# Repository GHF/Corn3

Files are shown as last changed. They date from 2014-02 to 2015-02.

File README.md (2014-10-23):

Corn3
=====
Copyright (C) 2014 Xo Wang

Corn3 is firmware for Corntroller version 3. It is a total rewrite of previous
Corntroller code, with a focus on writing code and documentation that may serve
as an introduction to three phase motor control for hobbyists.

Build
-----
Corn3 is written for use with GNU Tools for ARM Embedded Processors
(https://launchpad.net/gcc-arm-embedded).

To build, run make:

```
make
```

If you don't have arm-none-eabi in your PATH, specify its prefix in TRGT, e.g.:

```
make TRGT=~/gcc-arm-none-eabi-4_8-2014q3/bin/arm-none-eabi-
```

Hardware
--------
Corntroller is a small and efficient brushless motor controller.

Version 3.2 features:

  - 0.8 in by 1.6 in
  - STM32F3 microcontroller (ARM Cortex-M4 @ 72MHz)
  - TI DRV8301 gate driver, current sense amplifier, and buck converter
  - Three-phase inverter with SO8 N-FETs
  - Dual shunt current sense
  - Hall sensor inputs
  - Up to 30 V input voltage

No power figures available, but should be similar to hobby controllers of
similar size.

Hacking
-------
Corn3 and Corntroller are developed using the Black Magic Probe debugger.

See http://www.blacksphere.co.nz/main/blackmagic

Corntroller v3 has a 10-pin "mini" keyed JTAG header and a PicoBlade 4-pin
serial debug connector. The firmware does not yet support USB firmware
flashing.

License
-------
Corn3 is licensed under the MIT license with non-advertisement clause.

In compliance with the Apache license that ChibiOS configuration and low level
drivers are licensed under, the Apache License version 2.0 is included.

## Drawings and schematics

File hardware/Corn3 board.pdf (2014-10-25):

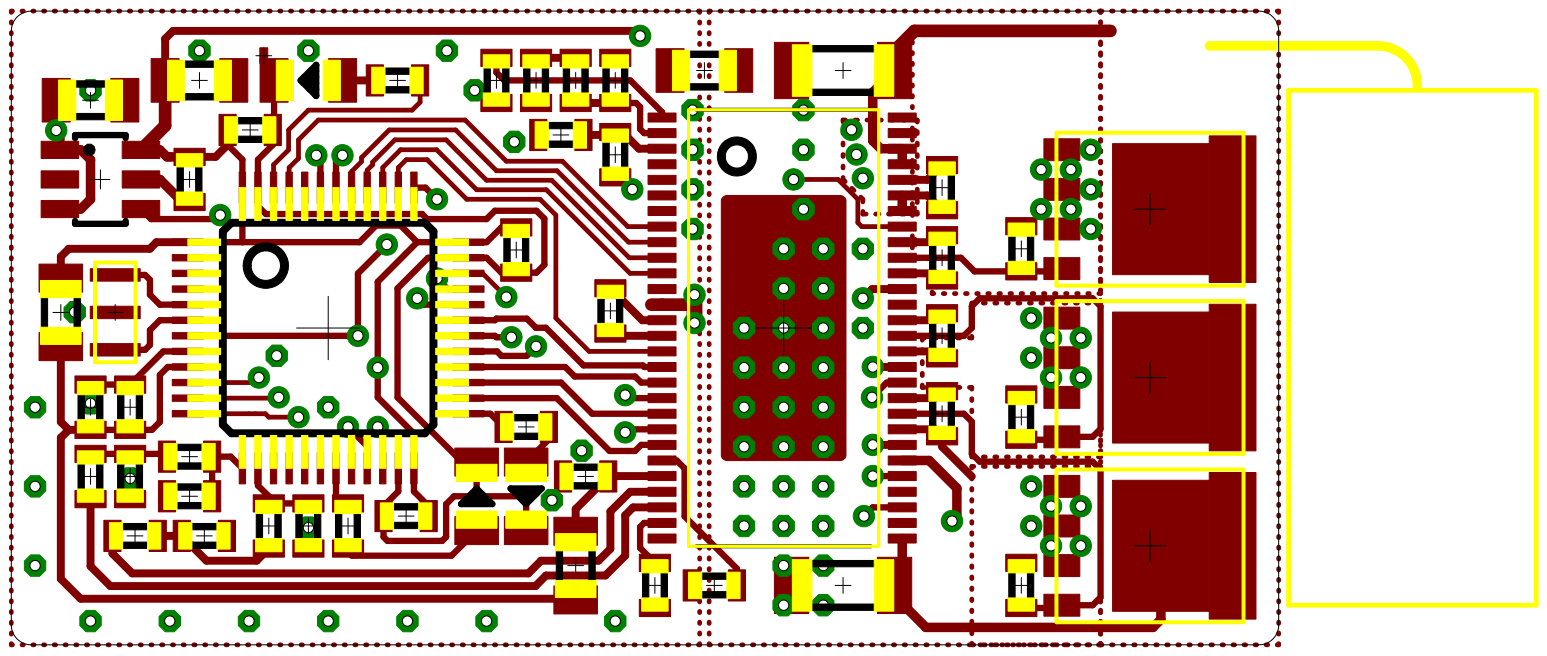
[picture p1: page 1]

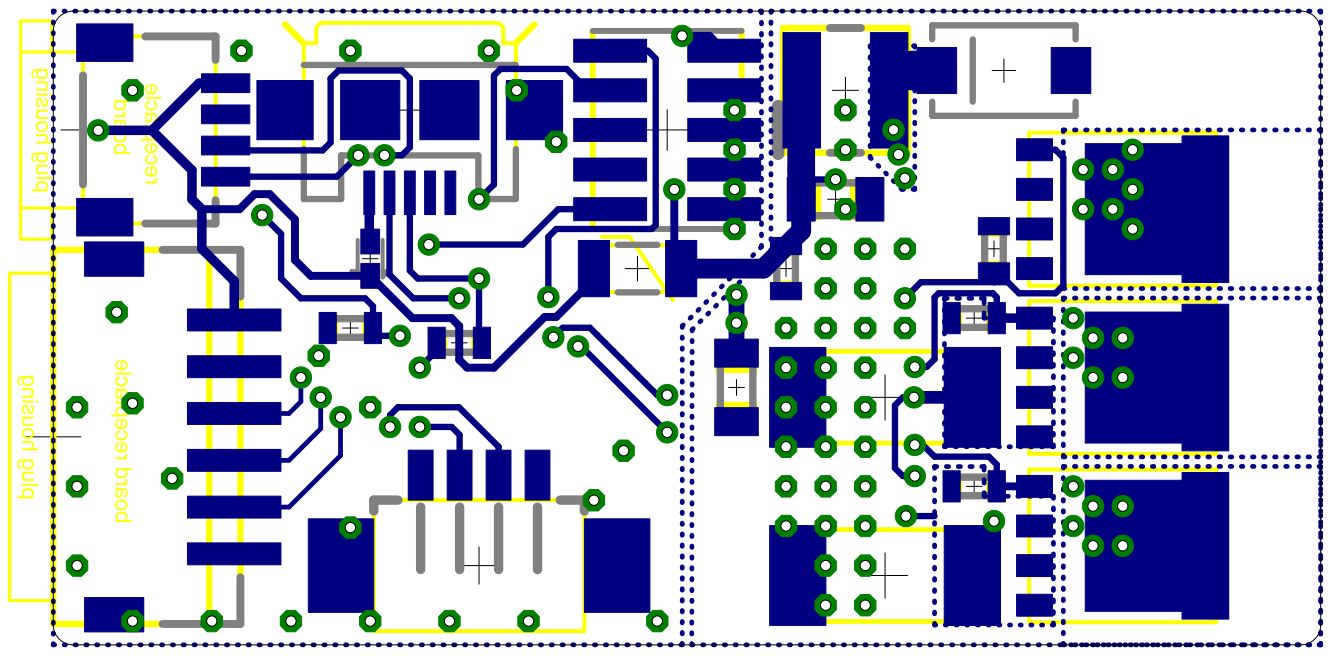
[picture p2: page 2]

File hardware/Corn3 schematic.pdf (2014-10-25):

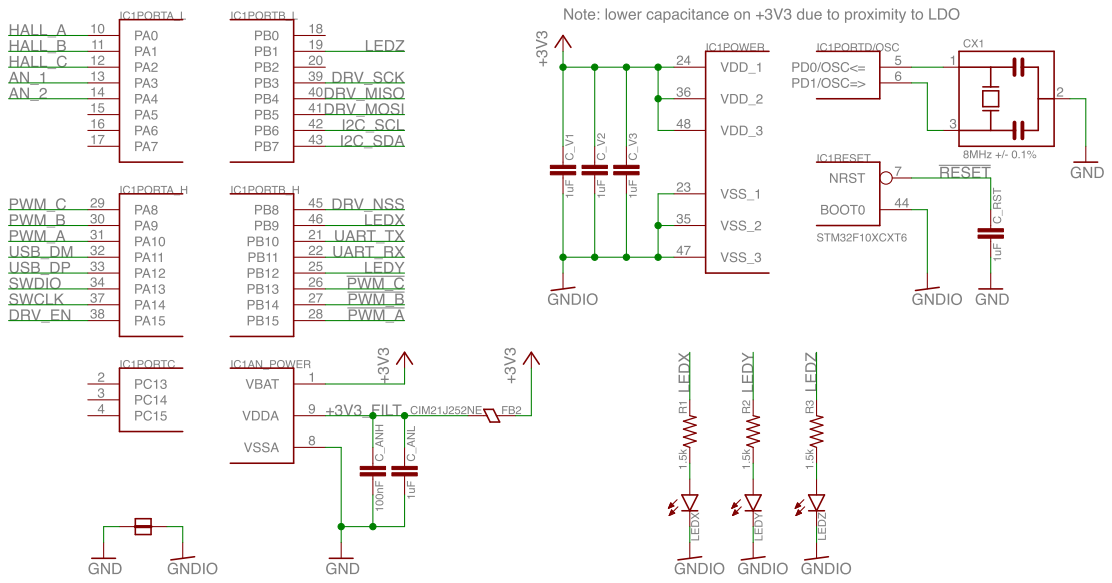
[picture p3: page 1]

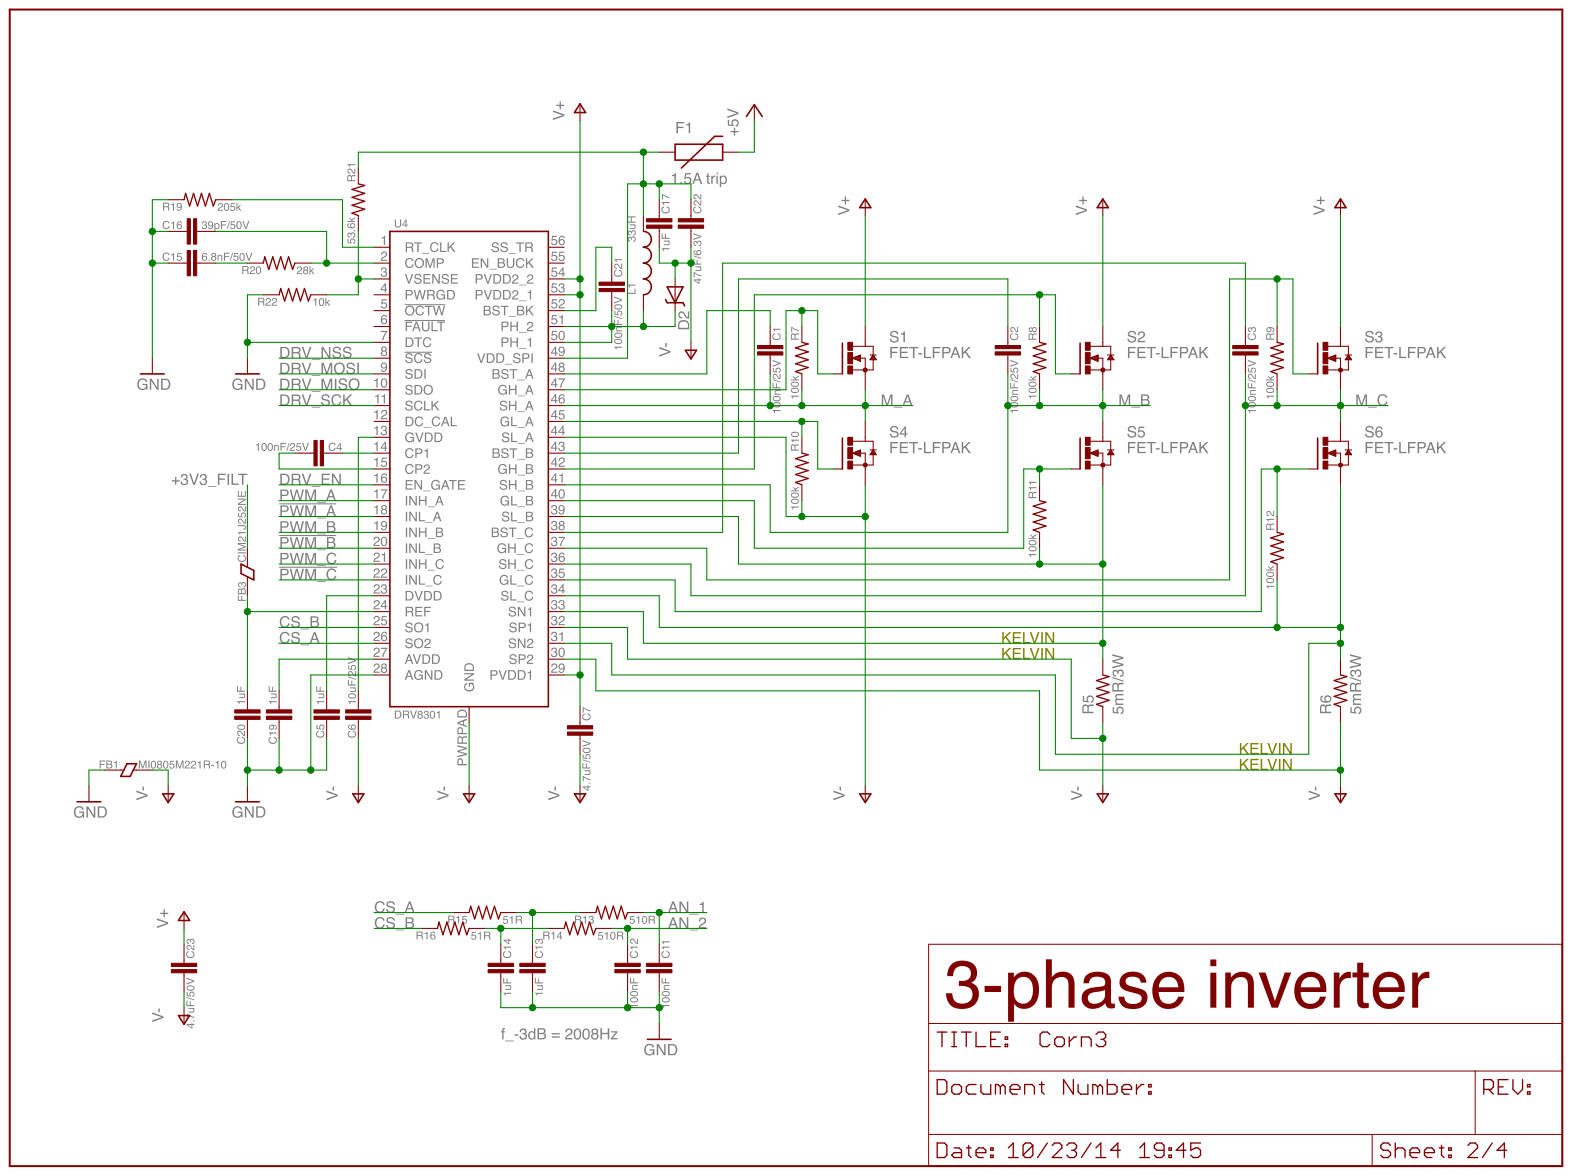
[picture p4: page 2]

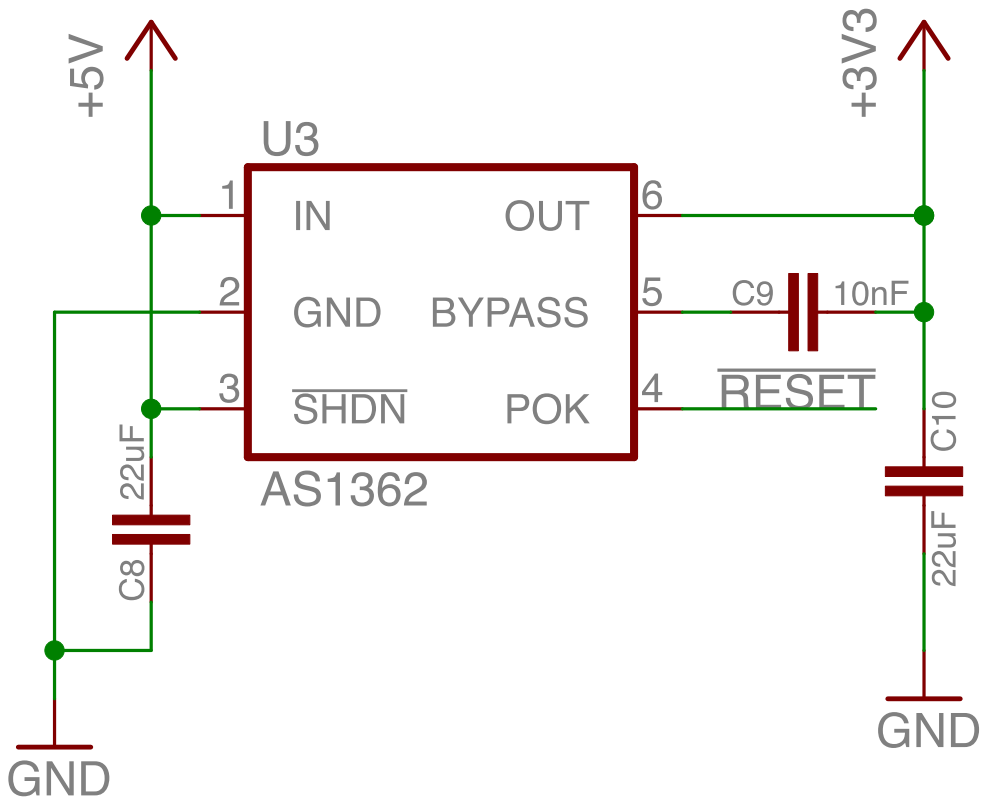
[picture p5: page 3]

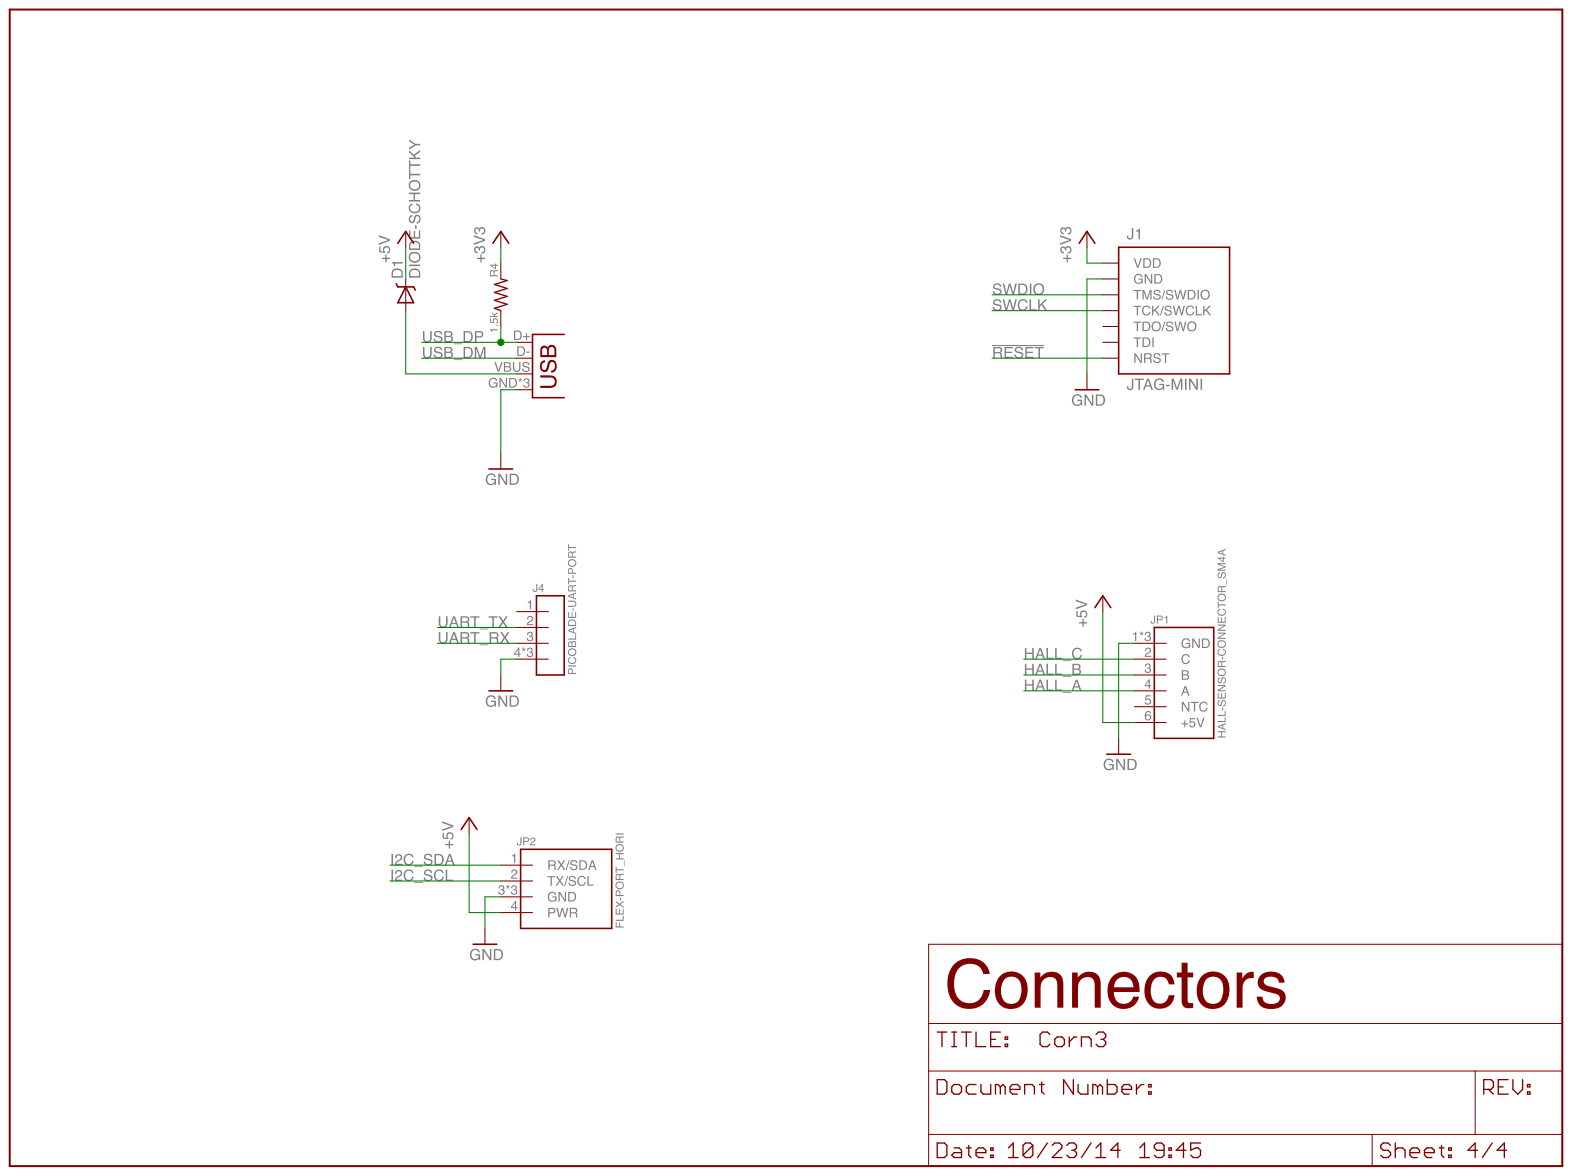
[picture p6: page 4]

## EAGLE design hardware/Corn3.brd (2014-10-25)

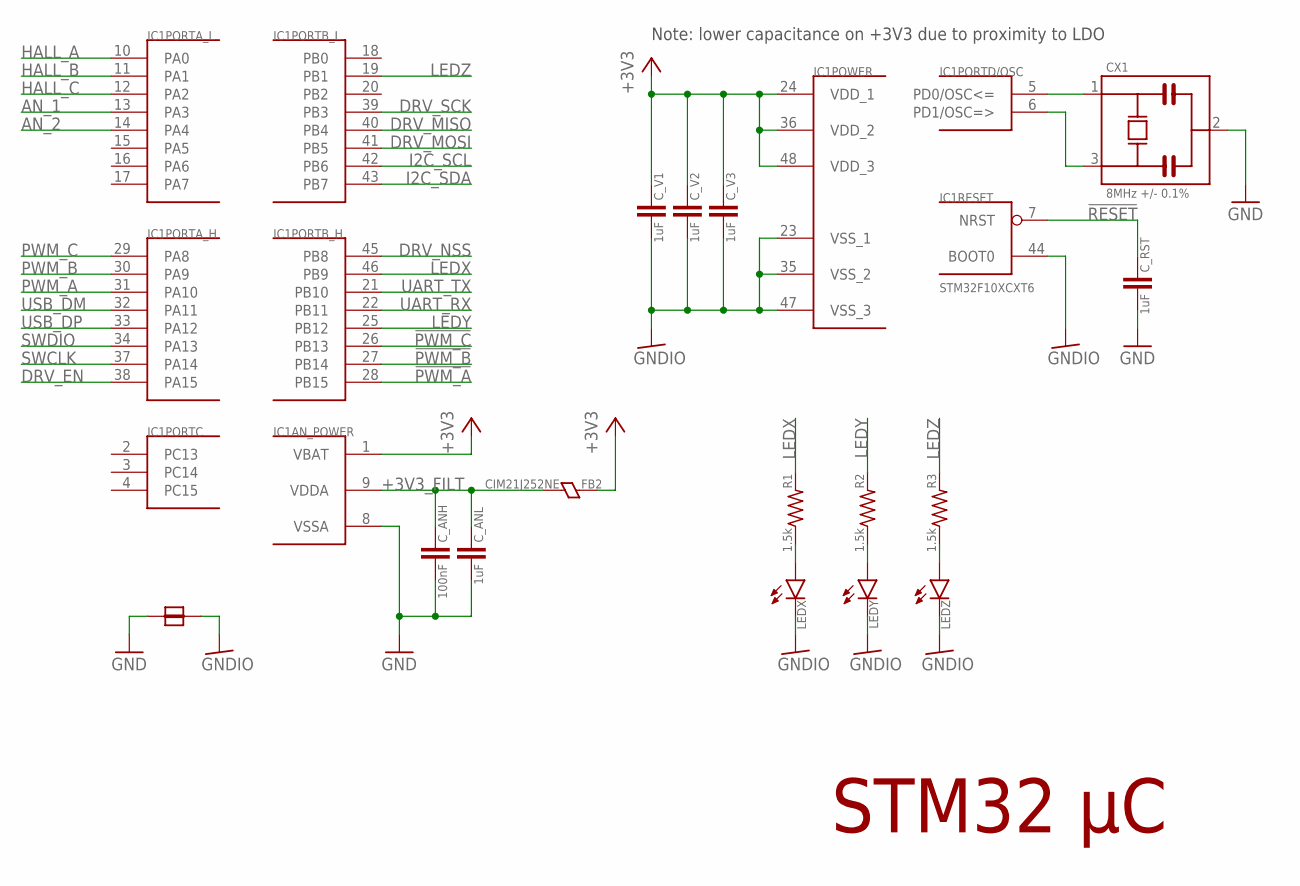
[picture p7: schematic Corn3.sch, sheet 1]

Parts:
CX1: 8MHz +/- 0.1%; MURATA_CSTCE
C_ANH: 100nF; 0603
C_ANL: 1uF; 0603
C_RST: 1uF; 0603
C_V1, C_V2, C_V3: 1uF; 0603
FB2: CIM21J252NE; 0805
IC1: STM32F10XCXT6; TQFP48
JUMPER-GND-GNDIO: JUMPER5025; 5025
LEDX: LED0805; 0805_POL
LEDY: LED0805; 0805_POL
LEDZ: LED0805; 0805_POL
R1, R2, R3: 1.5k; 0603

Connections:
!PWM_A: IC1.28 (PB15); also elsewhere on the board
!PWM_B: IC1.27 (PB14); also elsewhere on the board
!PWM_C: IC1.26 (PB13); also elsewhere on the board
!RESET: C_RST.1, IC1.7 (NRST); also elsewhere on the board
+3V3: C_V1.1, C_V2.1, C_V3.1, FB2.2, IC1.1 (VBAT), IC1.24 (VDD_1), IC1.36 (VDD_2), IC1.48 (VDD_3); also elsewhere on the board
+3V3_FILT: C_ANH.1, C_ANL.1, FB2.1, IC1.9 (VDDA); also elsewhere on the board
AN_1: IC1.13 (PA3); also elsewhere on the board
AN_2: IC1.14 (PA4); also elsewhere on the board
DRV_EN: IC1.38 (PA15); also elsewhere on the board
DRV_MISO: IC1.40 (PB4); also elsewhere on the board
DRV_MOSI: IC1.41 (PB5); also elsewhere on the board
DRV_NSS: IC1.45 (PB8); also elsewhere on the board
DRV_SCK: IC1.39 (PB3); also elsewhere on the board
GND: CX1.2, C_ANH.2, C_ANL.2, C_RST.2, IC1.8 (VSSA), JUMPER-GND-GNDIO.1; also elsewhere on the board
GNDIO: C_V1.2, C_V2.2, C_V3.2, IC1.23 (VSS_1), IC1.35 (VSS_2), IC1.44 (BOOT0), IC1.47 (VSS_3), JUMPER-GND-GNDIO.2, LEDX.- (C), LEDY.- (C), LEDZ.- (C)
HALL_A: IC1.10 (PA0); also elsewhere on the board
HALL_B: IC1.11 (PA1); also elsewhere on the board
HALL_C: IC1.12 (PA2); also elsewhere on the board
I2C_SCL: IC1.42 (PB6); also elsewhere on the board
I2C_SDA: IC1.43 (PB7); also elsewhere on the board
LEDX: IC1.46 (PB9), R1.2
LEDY: IC1.25 (PB12), R2.2
LEDZ: IC1.19 (PB1), R3.2
unnamed: CX1.3, IC1.6 (PD1/OSC=>)
unnamed: CX1.1, IC1.5 (PD0/OSC<=)
unnamed: LEDX.+ (A), R1.1
unnamed: LEDZ.+ (A), R3.1
unnamed: LEDY.+ (A), R2.1
PWM_A: IC1.31 (PA10); also elsewhere on the board
PWM_B: IC1.30 (PA9); also elsewhere on the board
PWM_C: IC1.29 (PA8); also elsewhere on the board
SWCLK: IC1.37 (PA14); also elsewhere on the board
SWDIO: IC1.34 (PA13); also elsewhere on the board
UART_RX: IC1.22 (PB11); also elsewhere on the board
UART_TX: IC1.21 (PB10); also elsewhere on the board
USB_DM: IC1.32 (PA11); also elsewhere on the board
USB_DP: IC1.33 (PA12); also elsewhere on the board

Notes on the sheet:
STM32 µC
Note: lower capacitance on +3V3 due to proximity to LDO

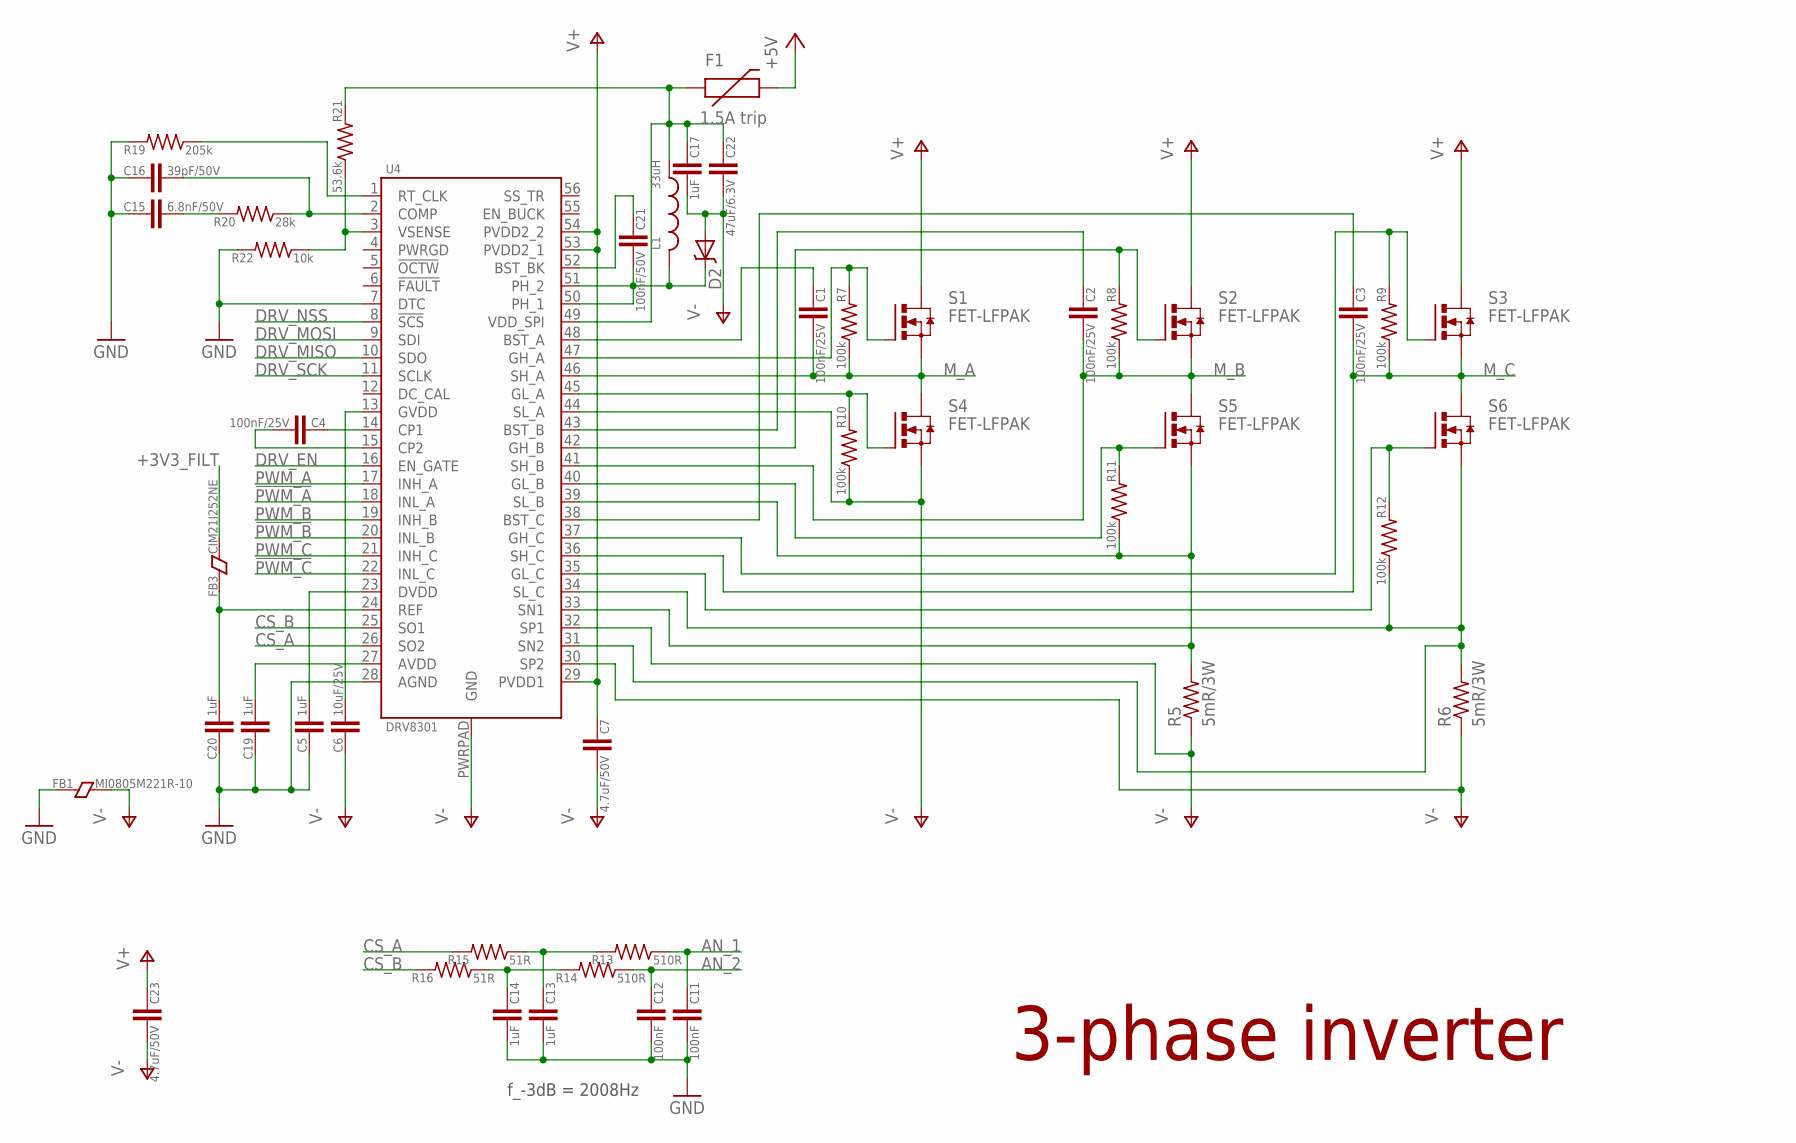
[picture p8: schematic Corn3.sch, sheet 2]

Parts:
C1, C2, C3, C4: 100nF/25V; 0603
C5, C13, C14, C17, C19, C20: 1uF; 0603
C6: 10uF/25V; 0805
C7, C23: 4.7uF/50V; 1206
C11, C12: 100nF; 0603
C15: 6.8nF/50V; 0603
C16: 39pF/50V; 0603
C21: 100nF/50V; 0603
C22: 47uF/6.3V; 0805
D2: DIODE-SCHOTTKY_; SMA-DIODE
F1: 1.5A trip; PTC-1206
FB1: MI0805M221R-10; 0805
FB3: CIM21J252NE; 0805
L1: 33uH; TAIYO-YUDEN_NR40
R5, R6: 5mR/3W; R2512
R7, R8, R9, R10, R11, R12: 100k; 0603
R13, R14: 510R; 0603
R15, R16: 51R; 0603
R19: 205k; 0603
R20: 28k; 0603
R21: 53.6k; 0603
R22: 10k; 0603
S1, S2, S3, S4, S5, S6: FET-LFPAK; SON-5X6
U4: DRV8301; HTSSOP-56

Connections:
!PWM_A: U4.18 (INL_A); also elsewhere on the board
!PWM_B: U4.20 (INL_B); also elsewhere on the board
!PWM_C: U4.22 (INL_C); also elsewhere on the board
+3V3_FILT: FB3.1; also elsewhere on the board
+5V: F1.2; also elsewhere on the board
AN_1: C11.1, R13.1; also elsewhere on the board
AN_2: C12.1, R14.1; also elsewhere on the board
CS_A: R15.2, U4.26 (SO2)
CS_B: R16.2, U4.25 (SO1)
DRV_EN: U4.16 (EN_GATE); also elsewhere on the board
DRV_MISO: U4.10 (SDO); also elsewhere on the board
DRV_MOSI: U4.9 (SDI); also elsewhere on the board
DRV_NSS: U4.8 (!SCS); also elsewhere on the board
DRV_SCK: U4.11 (SCLK); also elsewhere on the board
GND: C5.1, C11.2, C12.2, C13.2, C14.2, C15.1, C16.1, C19.1, C20.1, FB1.2, R19.2, R22.2, U4.7 (DTC), U4.28 (AGND); also elsewhere on the board
M_A: C1.2, R7.1, S1.S1 (S), S1.S2 (S), S1.S3 (S), S4.D, S4.D_ (D), U4.46 (SH_A)
M_B: C2.2, R8.1, S2.S1 (S), S2.S2 (S), S2.S3 (S), S5.D, S5.D_ (D), U4.41 (SH_B)
M_C: C3.2, R9.1, S3.S1 (S), S3.S2 (S), S3.S3 (S), S6.D, S6.D_ (D), U4.36 (SH_C)
unnamed: R8.2, S2.G, U4.42 (GH_B)
unnamed: R7.2, S1.G, U4.47 (GH_A)
unnamed: R12.2, S6.G, U4.35 (GL_C)
unnamed: R11.2, S5.G, U4.40 (GL_B)
unnamed: R9.2, S3.G, U4.37 (GH_C)
unnamed: C21.1, U4.52 (BST_BK)
unnamed: C1.1, U4.48 (BST_A)
unnamed: C2.1, U4.43 (BST_B)
unnamed: C3.1, U4.38 (BST_C)
unnamed: R10.2, S4.G, U4.45 (GL_A)
unnamed: C17.1, C22.1, F1.1, L1.1, R21.2, U4.49 (VDD_SPI)
unnamed: C16.2, R20.1, U4.2 (COMP)
unnamed: C14.1, R14.2, R16.1
unnamed: C13.1, R13.2, R15.1
unnamed: C15.2, R20.2
unnamed: R21.1, R22.1, U4.3 (VSENSE)
unnamed: C5.2, U4.23 (DVDD)
unnamed: C6.2, U4.13 (GVDD)
unnamed: C4.1, U4.14 (CP1)
unnamed: C4.2, U4.15 (CP2)
unnamed: C21.2, D2.C, L1.2, U4.50 (PH_1), U4.51 (PH_2)
unnamed: C20.2, FB3.2, U4.24 (REF)
unnamed: C19.2, U4.27 (AVDD)
unnamed: R19.1, U4.1 (RT_CLK)
PWM_A: U4.17 (INH_A); also elsewhere on the board
PWM_B: U4.19 (INH_B); also elsewhere on the board
PWM_C: U4.21 (INH_C); also elsewhere on the board
SL_B: R5.2, R11.1, S5.S1 (S), S5.S2 (S), S5.S3 (S), U4.33 (SN1), U4.39 (SL_B)
SL_C: R6.2, R12.1, S6.S1 (S), S6.S2 (S), S6.S3 (S), U4.31 (SN2), U4.34 (SL_C)
V+: C7.1, C23.1, S1.D, S1.D_ (D), S2.D, S2.D_ (D), S3.D, S3.D_ (D), U4.29 (PVDD1), U4.53 (PVDD2_1), U4.54 (PVDD2_2)
V-: C6.1, C7.2, C17.2, C22.2, C23.2, D2.A, FB1.1, R5.1, R6.1, R10.1, S4.S1 (S), S4.S2 (S), S4.S3 (S), U4.30 (SP2), U4.32 (SP1), U4.44 (SL_A), U4.PWRPAD (GND)

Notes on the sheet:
3-phase inverter
f_-3dB = 2008Hz

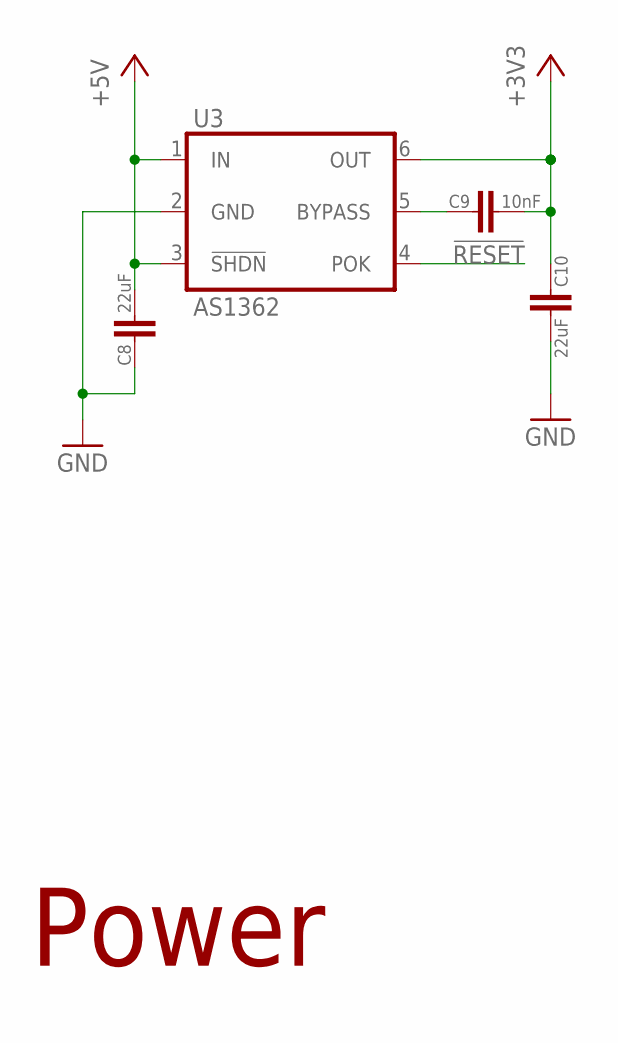
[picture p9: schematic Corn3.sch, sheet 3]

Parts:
C8, C10: 22uF; 0805
C9: 10nF; 0603
U3: AS1362; SOT23-6

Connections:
!RESET: U3.4 (POK); also elsewhere on the board
+3V3: C9.2, C10.1, U3.6 (OUT); also elsewhere on the board
+5V: C8.2, U3.1 (IN), U3.3 (!SHDN); also elsewhere on the board
GND: C8.1, C10.2, U3.2 (GND); also elsewhere on the board
unnamed: C9.1, U3.5 (BYPASS)

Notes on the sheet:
Power

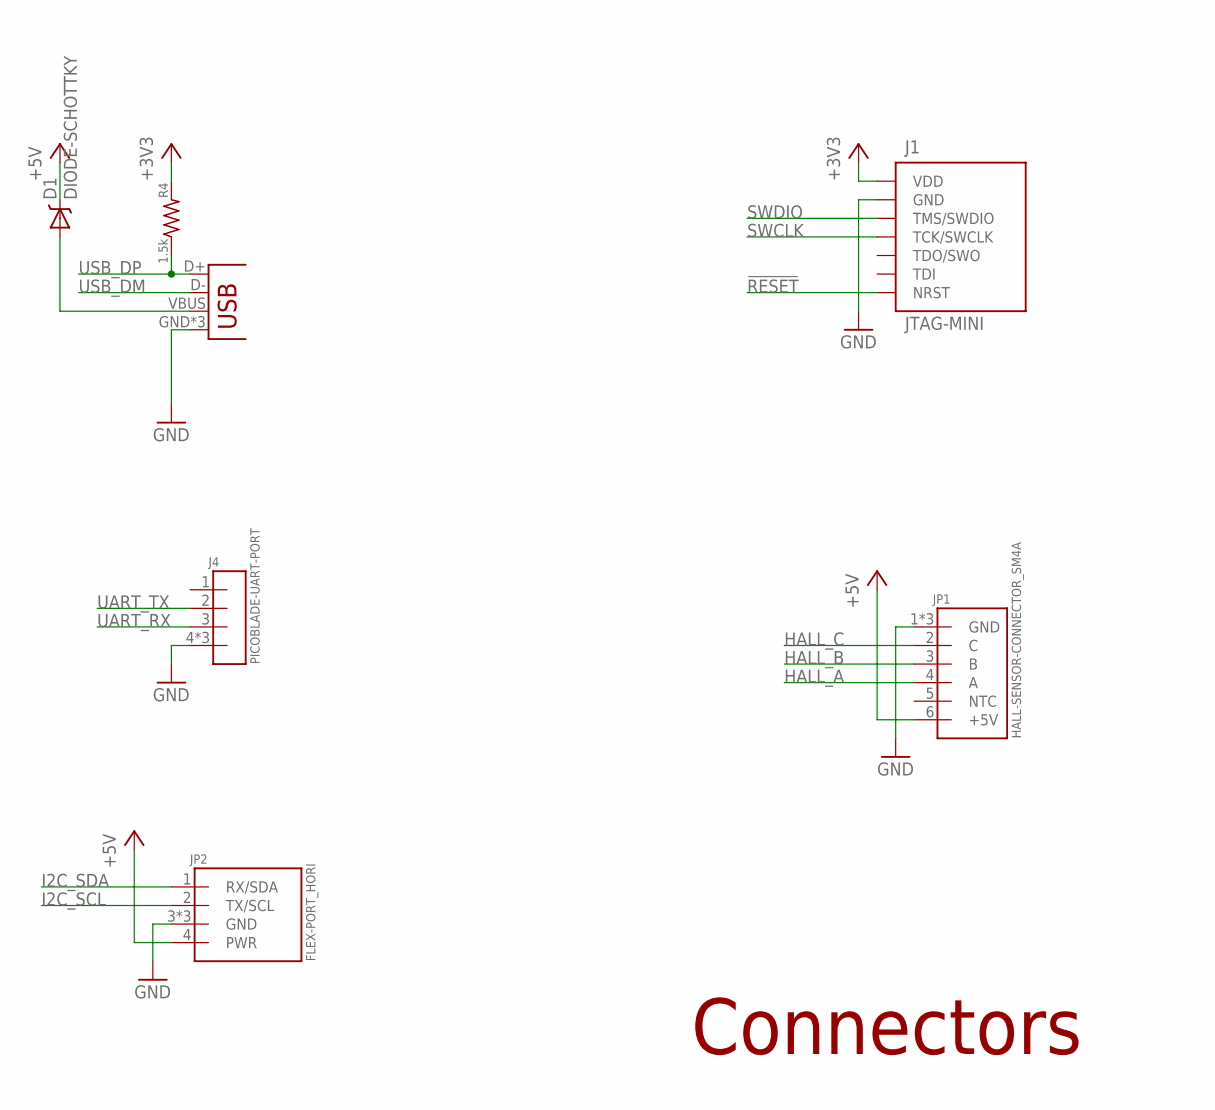
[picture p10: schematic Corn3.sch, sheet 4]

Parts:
D1: DIODE-SCHOTTKY; SOD-523
J1: JTAG-MINI
J4: PICOBLADE-UART-PORT; PICOBLADE-04-SMD-RA
JP1: HALL-SENSOR-CONNECTOR_SM4A; JST_S6B-ZR-SM4A
JP2: FLEX-PORT_HORI; JST_SM04B-SRSS
JP3: USB-MICROB
R4: 1.5k; 0603

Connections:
!RESET: J1.NRST; also elsewhere on the board
+3V3: J1.VDD, R4.2; also elsewhere on the board
+5V: D1.C, JP1.6 (+5V), JP2.4 (PWR); also elsewhere on the board
GND: J1.GND1 (GND), J1.GND2 (GND), J1.GND3 (GND), J1.GND4 (GND), J4.4, J4.TAB1 (4), J4.TAB2 (4), JP1.1 (GND), JP1.TAB1 (GND), JP1.TAB2 (GND), JP2.3 (GND), JP2.TAB1 (GND), JP2.TAB2 (GND), JP3.GND, JP3.MT1 (GND), JP3.MT2 (GND); also elsewhere on the board
HALL_A: JP1.4 (A); also elsewhere on the board
HALL_B: JP1.3 (B); also elsewhere on the board
HALL_C: JP1.2 (C); also elsewhere on the board
I2C_SCL: JP2.2 (TX/SCL); also elsewhere on the board
I2C_SDA: JP2.1 (RX/SDA); also elsewhere on the board
unnamed: D1.A, JP3.VBUS
SWCLK: J1.TCK (TCK/SWCLK); also elsewhere on the board
SWDIO: J1.TMS (TMS/SWDIO); also elsewhere on the board
UART_RX: J4.3; also elsewhere on the board
UART_TX: J4.2; also elsewhere on the board
USB_DM: JP3.D-; also elsewhere on the board
USB_DP: JP3.D+, R4.1; also elsewhere on the board

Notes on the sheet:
Connectors

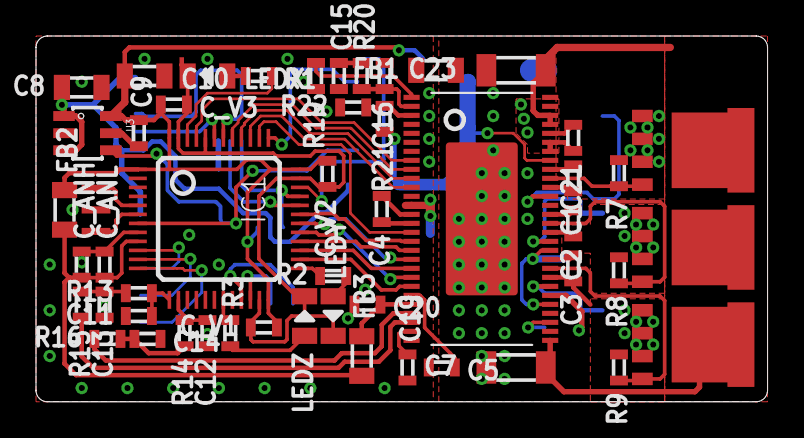
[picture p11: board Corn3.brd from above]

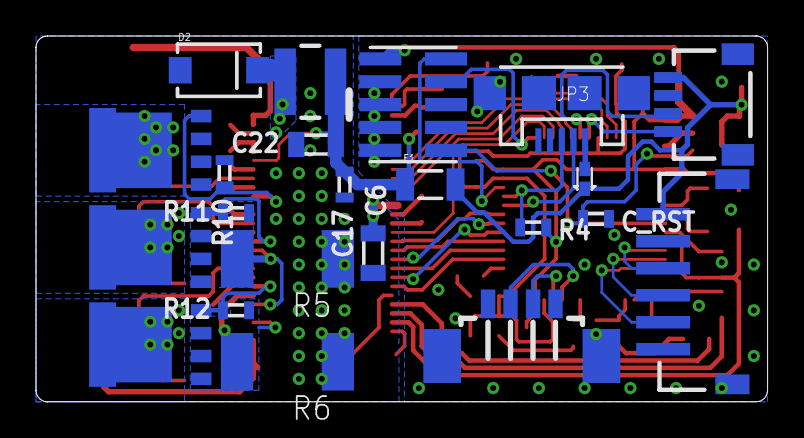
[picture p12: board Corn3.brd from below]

Board: 2 copper layers, 40.6 x 20.3 mm, 74 parts (22 on the bottom side), 73 nets.

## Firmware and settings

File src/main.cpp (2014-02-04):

/*
 * Corn3 - Copyright (C) 2014 Xo Wang
 *
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
 * Except as contained in this notice, the name(s) of the above copyright
 * holders shall not be used in advertising or otherwise to promote the sale,
 * use or other dealings in this Software without prior written authorization.
 */

#include <cstdlib>

#include "ch.h"
#include "hal.h"

#include "corn.h"

int main(void) {
  halInit();
  chSysInit();

  Corn corn;
  corn.Start();
  corn.MainLoop();

  return EXIT_SUCCESS;
}

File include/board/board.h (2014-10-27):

/*
 * Corn3 - Copyright (C) 2014 Xo Wang
 * ChibiOS/RT - Copyright (C) 2006-2013 Giovanni Di Sirio (MODIFIED BY ABOVE)
 *
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
 * Except as contained in this notice, the name(s) of the above copyright
 * holders shall not be used in advertising or otherwise to promote the sale,
 * use or other dealings in this Software without prior written authorization.
 */

#ifndef BOARD_BOARD_H_
#define BOARD_BOARD_H_

/*
 * Setup for the Corntroller brushless motor controller.
 */

/*
 * Board oscillators-related settings.
 * NOTE: LSE not fitted.
 */
#if !defined(STM32_LSECLK)
#define STM32_LSECLK                0
#endif

#define STM32_LSEDRV                (3 << 3)

#if !defined(STM32_HSECLK)
#define STM32_HSECLK                8000000
#endif

/*
 * MCU type as defined in the ST header.
 */
#define STM32F30X

/*
 * IO pins assignments.
 */
#define GPIOA_HALL_A                0
#define GPIOA_HALL_B                1
#define GPIOA_HALL_C                2
#define GPIOA_PIN3                  3
#define GPIOA_PIN4                  4
#define GPIOA_PIN5                  5
#define GPIOA_PIN6                  6
#define GPIOA_PIN7                  7
#define GPIOA_PWM_C                 8
#define GPIOA_PWM_B                 9
#define GPIOA_PWM_A                 10
#define GPIOA_USB_DM                11
#define GPIOA_USB_DP                12
#define GPIOA_SWDIO                 13
#define GPIOA_SWCLK                 14
#define GPIOA_DRV_EN                15

#define GPIOB_PIN0                  0
#define GPIOB_LEDZ                  1
#define GPIOB_PIN2                  2
#define GPIOB_DRV_SCK               3
#define GPIOB_DRV_MISO              4
#define GPIOB_DRV_MOSI              5
#define GPIOB_PWM_IN                6
#define GPIOB_PIN7                  7
#define GPIOB_DRV_NSS               8
#define GPIOB_LEDX                  9
#define GPIOB_UART_TX               10
#define GPIOB_UART_RX               11
#define GPIOB_LEDY                  12
#define GPIOB_PWM_CN                13
#define GPIOB_PWM_BN                14
#define GPIOB_PWM_AN                15

#define GPIOC_PIN0                  0
#define GPIOC_PIN1                  1
#define GPIOC_PIN2                  2
#define GPIOC_PIN3                  3
#define GPIOC_PIN4                  4
#define GPIOC_PIN5                  5
#define GPIOC_PIN6                  6
#define GPIOC_PIN7                  7
#define GPIOC_PIN8                  8
#define GPIOC_PIN9                  9
#define GPIOC_PIN10                 10
#define GPIOC_PIN11                 11
#define GPIOC_PIN12                 12
#define GPIOC_PIN13                 13
#define GPIOC_PIN14                 14
#define GPIOC_PIN15                 15

#define GPIOD_PIN0                  0
#define GPIOD_PIN1                  1
#define GPIOD_PIN2                  2
#define GPIOD_PIN3                  3
#define GPIOD_PIN4                  4
#define GPIOD_PIN5                  5
#define GPIOD_PIN6                  6
#define GPIOD_PIN7                  7
#define GPIOD_PIN8                  8
#define GPIOD_PIN9                  9
#define GPIOD_PIN10                 10
#define GPIOD_PIN11                 11
#define GPIOD_PIN12                 12
#define GPIOD_PIN13                 13
#define GPIOD_PIN14                 14
#define GPIOD_PIN15                 15

#define GPIOE_PIN0                  0
#define GPIOE_PIN1                  1
#define GPIOE_PIN2                  2
#define GPIOE_PIN3                  3
#define GPIOE_PIN4                  4
#define GPIOE_PIN5                  5
#define GPIOE_PIN6                  6
#define GPIOE_PIN7                  7
#define GPIOE_PIN8                  8
#define GPIOE_PIN9                  9
#define GPIOE_PIN10                 10
#define GPIOE_PIN11                 11
#define GPIOE_PIN12                 12
#define GPIOE_PIN13                 13
#define GPIOE_PIN14                 14
#define GPIOE_PIN15                 15

#define GPIOF_OSC_IN                0
#define GPIOF_OSC_OUT               1
#define GPIOF_PIN2                  2
#define GPIOF_PIN3                  3
#define GPIOF_PIN4                  4
#define GPIOF_PIN5                  5
#define GPIOF_PIN6                  6
#define GPIOF_PIN7                  7
#define GPIOF_PIN8                  8
#define GPIOF_PIN9                  9
#define GPIOF_PIN10                 10
#define GPIOF_PIN11                 11
#define GPIOF_PIN12                 12
#define GPIOF_PIN13                 13
#define GPIOF_PIN14                 14
#define GPIOF_PIN15                 15
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

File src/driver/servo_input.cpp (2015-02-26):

/*
 * Corn3 - Copyright (C) 2014 Xo Wang
 *
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
 * Except as contained in this notice, the name(s) of the above copyright
 * holders shall not be used in advertising or otherwise to promote the sale,
 * use or other dealings in this Software without prior written authorization.
 */

#include "driver/servo_input.h"

#include <algorithm>

#include "config.h"
#include "base/integer.h"
#include "base/log.h"
#include "base/utility.h"
#include "motor/commutator_six_step.h"

ServoInput::ServoInput(ICUDriver *icu_driver)
    : icu_driver_(icu_driver),
      commutator_six_step_(nullptr),
      num_overflows_(0),
      last_amplitude_(0) {
}

void ServoInput::Start() {
  icu_driver_->self = this;
  LogDebug("Configuring servo input capture at %u Hz...", SERVO_INPUT_ICU_FREQ);
  icuStart(icu_driver_, &kServoIcuConfig);
  icuEnable(icu_driver_);
  LogInfo("Started servo input capture.");
}

constexpr int ServoInput::kInputLow;
constexpr int ServoInput::kInputHigh;
constexpr int ServoInput::kInputDeadband;
constexpr int ServoInput::kInputMargin;
constexpr int ServoInput::kInputSlewLimit;

const ICUConfig ServoInput::kServoIcuConfig = { ICU_INPUT_ACTIVE_HIGH,
                                                SERVO_INPUT_ICU_FREQ,
                                                IcuWidthCallback,
                                                IcuPeriodCallback,
                                                IcuOverflowCallback,
                                                ICU_CHANNEL_1,
                                                0,
                                                ICU_RESET_ON_ACTIVE,
                                                ICU_CHANNEL_1_INPUT_1,
                                                ICU_FILTER_F_1_N_8 };

void ServoInput::HandlePulse(int width, int period, bool valid) {
  if (commutator_six_step_ != nullptr) {
    if ((width < (kInputLow - kInputMargin)) ||
        (width > (kInputHigh + kInputMargin))) {
      valid = false;
    }
    if (valid) {
      const int bounded_command = Clamp(width, kInputLow, kInputHigh);
      const Width16 period_2 = commutator_six_step_->GetMaxAmplitude();
      const Width16Diff amplitude = MapRange(kInputLow,
                                             kInputHigh,
                                             bounded_command,
                                             -period_2,
                                             period_2,
                                             kInputDeadband);
      // Greatest change allowed this period based on slew rate limits.
      const int slew_margin = (kInputSlewLimit * period) /
                              (SERVO_INPUT_ICU_FREQ / 1000);
      const Width16Diff slew_limited_amplitude =
          Clamp<int>(amplitude,
                     last_amplitude_ - slew_margin,
                     last_amplitude_ + slew_margin);
      commutator_six_step_->WriteAmplitude(slew_limited_amplitude);
      last_amplitude_ = slew_limited_amplitude;
      chSysLockFromIsr();
      commutator_six_step_->SetEnable(true);
      commutator_six_step_->SignalChange();
      chSysUnlockFromIsr();
    } else {
      last_amplitude_ = 0;
      chSysLockFromIsr();
      commutator_six_step_->SetEnable(false);
      commutator_six_step_->SignalChange();
      chSysUnlockFromIsr();
    }
  }
}

// Gets width of pulse captured. Disables drive if time between edges overflowed
// the timer counter.
void ServoInput::IcuWidthCallback(ICUDriver *icu_driver) {
  const uint16_t pulse_width = icuGetWidth(icu_driver);
  const uint16_t pulse_period = icuGetPeriod(icu_driver);
  ServoInput * const servo_input = static_cast<ServoInput *>(icu_driver->self);
  if (servo_input->num_overflows_ > 0) {
    servo_input->HandlePulse(-1, -1, false);
  } else {
    servo_input->HandlePulse(pulse_width, pulse_period, true);
  }
}

// Resets counter for timer overflows since pulse positive edge.
void ServoInput::IcuPeriodCallback(ICUDriver *icu_driver) {
  static_cast<ServoInput *>(icu_driver->self)->num_overflows_ = 0;
}

// Disables commutation if more than one overflow has ocurred.
void ServoInput::IcuOverflowCallback(ICUDriver *icu_driver) {
  ServoInput * const servo_input = static_cast<ServoInput *>(icu_driver->self);
  // Increment with saturation.
  servo_input->num_overflows_ =
      std::max(servo_input->num_overflows_, servo_input->num_overflows_ + 1);
  if (servo_input->num_overflows_ > 0) {
    servo_input->HandlePulse(-1, -1, false);
  }
}

int32_t ServoInput::MapRange(int32_t in_low, int32_t in_high, int32_t value,
                             int32_t out_low, int32_t out_high,
                             int32_t deadband) {
  // Center the input range on zero.
  const int32_t in_center = Average(in_low, in_high);
  int32_t centered_input = value - in_center;

  // Cut away the deadband from the centered input.
  if (Nabs(centered_input) > -deadband) {
    centered_input = 0;
  } else {
    centered_input -= SignOf(centered_input) * deadband;
  }

  // Compute the length of input and output ranges.
  const int32_t inScale = in_high - in_low - 2 * deadband;
  const int32_t outScale = out_high - out_low;
  const int32_t outCenter = Average(out_low, out_high);

  // Scale by output to input ratio, then shift from zero into range.
  // WARNING: this computation can easily overflow!
  const int32_t outValue = centered_input * outScale / inScale + outCenter;

  // Clamp output within range.
  return std::max(out_low, std::min(out_high, outValue));
}

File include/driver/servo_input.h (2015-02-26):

/*
 * Corn3 - Copyright (C) 2014 Xo Wang
 *
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
 * Except as contained in this notice, the name(s) of the above copyright
 * holders shall not be used in advertising or otherwise to promote the sale,
 * use or other dealings in this Software without prior written authorization.
 */

#ifndef DRIVER_SERVO_INPUT_H_
#define DRIVER_SERVO_INPUT_H_

#include "hal.h"

#include "config.h"

class CommutatorSixStep;

/**
 * @brief Driver for reading and processing servo PWM signals into throttle
 *        commands, and optionally sending them to the motor commutator.
 */
class ServoInput {
 public:
  /**
   * @brief Creates a driver structure for handling RC servo pulse input as
   *        a throttle for the commutation.
   *
   * @param icu_driver OS driver for capturing servo input edges.
   */
  ServoInput(ICUDriver *icu_driver);

  /**
   * @brief Starts capturing and processing servo PWM input.
   */
  void Start();

  /**
   * @brief Connects a commutator as an output for the servo signals being read.
   *
   * @param commutator_six_step Motor driving sequencer.
   */
  void SetCommutatorSixStep(CommutatorSixStep *commutator_six_step) {
    commutator_six_step_ = commutator_six_step;
  }

 protected:
  /// Lower bound of pulse width.
  static constexpr int kInputLow = SERVO_INPUT_MIN_COMMAND;
  /// Upper bound of pulse width.
  static constexpr int kInputHigh = SERVO_INPUT_MAX_COMMAND;
  /// Deadband of pulse width.
  static constexpr int kInputDeadband = SERVO_INPUT_DEADBAND;
  /// Margin past the bounds for which pulse widths are rejected.
  static constexpr int kInputMargin = SERVO_INPUT_MARGIN;
  /// Maximum motor command rate of change in amplitude units per millisecond.
  static constexpr int kInputSlewLimit = SERVO_INPUT_SLEW_LIMIT;
  /// Servo input capture settings.
  static const ICUConfig kServoIcuConfig;

  /**
   * @brief Handles servo pulse event.
   *
   * @param width Width of the pulse captured. Not used if @p valid is false.
   * @param period Period of the pulse captured. Not used if @p valid is false.
   * @param valid True if @p width is valid. Invalid can mean a pulse glitch,
   *              timeout, etc.
   */
  void HandlePulse(int width, int period, bool valid);

  /**
   * @brief Handles servo pulse input falling edges.
   *
   * @param icu_driver Input capture OS driver that originated the callback.
   */
  static void IcuWidthCallback(ICUDriver *icu_driver);

  /**
   * @brief Handles servo pulse input rising edges.
   *
   * @param icu_driver Input capture OS driver that originated the callback.
   */
  static void IcuPeriodCallback(ICUDriver *icu_driver);

  /**
   * @brief Handles servo pulse input unit timer overflows.
   *
   * @param icu_driver Input capture OS driver that originated the callback.
   */
  static void IcuOverflowCallback(ICUDriver *icu_driver);

  /**
   * @brief Maps one range of values linearly to another, with deadband.
   *
   * @note This does not check if inputs are valid.
   *
   * @note Deadband is a region at the center of the input range that is mapped
   *       to the center of the output range. Also, the rest of the input range
   *       will start at the extents of the deadband.
   *
   * @note Care must be taken to not exceed integer limits in this computation!
   *
   * TODO(Xo): Describe conditions that cause integer overflow errors.
   *
   * @param in_low Input range lower bound. @p value can not be less than this.
   * @param in_high Input range upper bound. @p value can not exceed this. Must
   *                be greater than @p in_low by twice @p deadband.
   * @param value Input value to map.
   * @param out_low Output range lower bound.
   * @param out_high Output range upper bound. Must be greater than @p out_low.
   * @param deadband Distance from center of input range for which all input
   *  values are mapped to "zero" (center of the output range).
   * @return Mapped input value after adjusting for deadband.
   */
  static int32_t MapRange(int32_t in_low, int32_t in_high, int32_t value,
                          int32_t out_low, int32_t out_high, int32_t deadband);

  ICUDriver * const icu_driver_;  ///< Timer input capture driver.
  CommutatorSixStep *commutator_six_step_;  ///< Servo commands signal sink.
  int num_overflows_;  ///< Times the timer overflowed since last edge.
  int last_amplitude_;  ///< Previous command sent to motor.
};

#endif  /* DRIVER_SERVO_INPUT_H_ */

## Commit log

2014-01-19 Initial commit of configuration and build files.
    Functionality is blinking the heartbeat LED.
2014-01-20 Add hardware design files.
    [Corn3.brd, Corn3.sch]
2014-01-20 Add UART capability.
2014-01-20 Add newlib-required syscalls to enable printf.
2014-01-20 Move board files to subdirectories in include and src.
2014-01-21 Add input capture driver to "lld" subdir.
    Copied from ChibiOS's ICU low-level driver (lld) for STM32.
2014-01-21 Strip input capture support for timers other than TIM2.
2014-01-21 Add 32-bit timer support to input capture driver.
2014-01-21 Add inputs XOR option to input capture driver.
2014-01-22 Add initialization timer, tweak LEDs.
2014-01-23 Add option to disable printf floating point support.
    Works by replacing newlib's double to string routine with a minimal stub.
2014-01-23 Allow base/logging to use chprintf instead of system printf.
2014-01-23 Add __dso_handle and disable thread-safe static initialization.
    This allows static objects to be defined.
2014-01-23 Print function name when logging.
2014-01-26 Add reset options and channels 3 & 4 to ICU driver.
    [icu_lld.c, icu_lld.h]
2014-01-27 Add workaround to ICU driver for timing issues.
    This makes the WAITING to ACTIVE transition generate a callback, and always clears the timer when enabling the ICU.
    [icu_lld.c, icu_lld.h]
2014-01-27 Add color reset at beginning of welcome message.
    [corn.cpp]
2014-01-27 Add Hall-effect sensor rotor angle driver.
    This represents the beginnings of the motor module. Also enable ICU driver 2 in the OS, which this driver relies on.
2014-01-27 Fix include order per style.
    [main.cpp]
2014-01-30 Flip hall sensor bits.
    [rotor_hall.cpp]
2014-01-30 Fix backslashes in config per style.
    [config.h]
2014-01-30 Disable UART flow control.
2014-01-30 Set error LED upon CriticalHalt.
2014-02-02 Add DRV8303 configuration and error detection driver.
    [DRV8303.cpp, DRV8303.h, config.h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]
2014-02-02 Fix PWM pin modes to not create spurious inverter spikes on init.
    [board.h]
2014-02-02 Add simple software filter for spurious hall edges.
    Also minor style change in constructor.
2014-02-02 Update ChibiOS and integrate changes to custom ICU low-level driver.
2014-02-03 Add PWM driver and inverter control interface.
    Driver has support for high impedance phases and deadtime insertion.
2014-02-03 Move PWM low level driver to lld dirs for customization.
2014-02-03 Make PWM generation center-aligned.
    Add cr1 field to PWM low level driver configuration.
2014-02-03 Add system reset functionality (two ^Cs over the debug serial).
    Add references to NVIC_SystemReset so it isn't optimized out and can be jumped to with the debugger.
    Minor changes per style.
    [corn.cpp]
2014-02-03 Separate driver initialization to separate Start functions.
    Rename DRV8303 methods to avoid confusion with "Start."
    [DRV8303.cpp, DRV8303.h, corn.cpp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]
2014-02-04 Fix channel B not being disabled bug.
    [inverter_pwm.cpp]
2014-02-04 Reverse bits of hall sensor state to match hardware.
    [rotor_hall.cpp]
2014-02-04 Add six-step commutation (motor-driving) logic.
2014-02-04 Undo hall sensor bit reverse and fix look up tables instead.
    Change naming per style.
    [rotor_hall.cpp]
2014-02-05 Fix RotorHall not recognizing timer overflows.
    [rotor_hall.cpp]
2014-02-07 Add servo PWM input driver.
    Changes and fixes to input capture driver. Add integer math header to base. Edit board files for PWM input rather than I2C.
    [board.h, config.h, corn.cpp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]
2014-02-07 Add full braking when throttle is zero.
2014-02-08 Disable motor drive when servo input capture times out.
2014-02-08 Poll gate driver for errors and reset as needed to clear errors.
    [DRV8303.cpp, corn.cpp]
2014-08-04 Update ChibiOS and merge new Makefile options.
    Remove references to FW lib.
    Merge in fix to PWM LLD; merge ignored for ICU LLD because TIM9 isn't supported.
    [pwm_lld.c]
2014-09-06 Fix AS1362 silkscreen first pin mark (#3).
    Increase hardware rev to 3.1. Add labels for motor phases.
    [Corn3.brd, Corn3.sch]
2014-09-06 Fix LED silkscreen polarity markings (#2).
    [Corn3.brd, Corn3.sch]
2014-09-06 Add diode from USB V+ to +5V (#1).
    [Corn3.brd, Corn3.sch]
2014-10-03 Add completed hardware v3.2 (#1, #4, #23, #24, #25).
    [Corn3.brd, Corn3.sch]
2014-10-06 Update ChibiOS to latest (2.6.x and then some).
    Merge PWM and ICU changes to custom low-level drivers.
2014-10-19 Fix APB2 clock to run at the correct 72MHz.
    [mcuconf.h]
2014-10-23 Update board config and README for hardware v3.2.
2014-10-23 Print project and version when starting build.
2014-10-24 Start hardware v3.3. Unserpentine SWCLK trace (#30).
    [Corn3.brd]
2014-10-24 Fix reversed Hall connector (#31) and change pinout for flex port.
    [Corn3.brd, Corn3.sch]
2014-10-25 Update to hardware v3.3.
    Slight changes to graphics (version, vanity, and copyright).
    [Corn3.brd]
2014-10-26 Fix system calls.
    Rename syscalls.c to not conflict with ChibiOS provided source.
    All calls implement the reentrant variety.
    Make _sbrk (now _sbrk_r) is safe to call from ISRs.
    Remove unnecessary syscalls.
    [corn.cpp]
2014-10-27 Add USB support.
    Initialize USB CDC ACM device as an OS serial channel.
    Add device version macros and an ARRAY_SIZE utility macro.
2015-02-20 Add input capture hardware filtering support.
    Enabled with defaults for servo input and hall sensor input.
2015-02-24 Add servo input bounds checking.
    No pulse width beyond a margin past the servo input mapping endpoint is
    accepted as a valid servo input.
2015-02-24 Add Clamp function.
2015-02-24 Reset timer counter at start of each servo pulse.
    Servo pulses are now zero-based so the capture register values are
    directly usable without overflow logic or rebasing against the previous
    falling edge capture.
    [servo_input.cpp, servo_input.h]
2015-02-26 Add motor command slew rate limiting to servo input.

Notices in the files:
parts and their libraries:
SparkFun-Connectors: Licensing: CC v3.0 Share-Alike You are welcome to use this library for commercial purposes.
